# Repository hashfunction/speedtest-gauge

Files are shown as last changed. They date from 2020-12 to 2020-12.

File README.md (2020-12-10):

# Treat Yourself to a Hack Day: Make a Physical Speedtest Gauge

Sure you love taking a Speedtest, but have you ever seen the results manifest in a 3D statue that lives on your desk? Now’s your chance. This repo contains everything you need to construct and program an ethernet-enabled physical Speedtest Gauge. All you’ll need to build it is access to a 3D printer, some affordable and easy-to-find parts, and a basic working knowledge of both electronics and command line interface (CLI) tools. Then you can proudly display your Speedtest gauge on your desk or gift it to a friend who also loves to nerd out over networks. Either way, you’ll have the most fun setup for measuring network throughput in town.

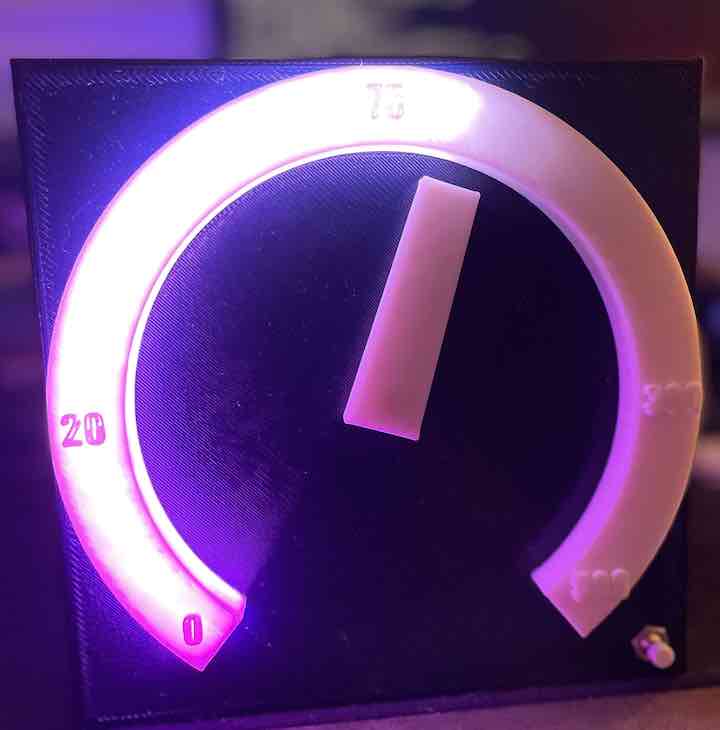
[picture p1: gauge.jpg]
Speedtest Gauge


## Components you’ll need
The total cost of all the components below is around $65, and the project will take about two or three hours to complete, not counting the time to 3D print the enclosure. 

This project requires the following components to work:

* A soldering iron. A basic one should do fine. 
* [Jumper wires](https://smile.amazon.com/REXQualis-120pcs-Breadboard-Arduino-Raspberry/dp/B072L1XMJR) to connect the various components together.
* A stepper motor. This project used [this model](https://smile.amazon.com/ELEGOO-28BYJ-48-ULN2003-Stepper-Arduino/dp/B01CP18J4A/) but feel free to upgrade to a better one. The limitation of this one is that the max speed is slow and so the gauge needle is not very quick.
* Programmable LED lights. This project uses [three neopixel ring lights](https://www.adafruit.com/product/1768). Note that you will need three of these to form the full gauge. You can find cheaper versions of this ring elsewhere.
* Physical buttons. A good candidate for buttons are these [mini push buttons](https://smile.amazon.com/gp/product/B0752RMB7Q/). 
* A [Raspberry Pi](https://www.adafruit.com/category/105). This drives the LED lights as well as the motor and runs the actual test. 
* A good [power source](https://smile.amazon.com/Raspberry-Power-Supply-Off-Switch/dp/B083JCL6H2) for the Raspberry Pi. 
* The 3D-printed housing. The housing and needle are where you finally get to put everything together. The STL printable files can be found on this GitHub project. 
* The free [Speedtest CLI](https://www.speedtest.net/apps/cli). The latest version of the official Speedtest CLI is used to actually run the network performance test. 
* Unbuffer. This is needed to parse the Speedtest CLI output. You can install it by running ```apt-get install expect```

## How to assemble your Speedtest gauge

* Step 1: Print out the housing using a 3D printer. The instructions can be found in this GitHub project. 

* Step 2: Attach the stepper motor to the center of the 3D-printed housing. Then attach the stepper motor driver to the motor, attach the +5V and GND on the controller to the appropriate Raspberry Pi GPIO pin. 

* Step 3: Attach the needle to the tip of the stepper motor. You can snap them together with some glue. 

* Step 4: Connect the controller to the Raspberry Pi with the following GPIO mappings:

    > IN1 to GPIO17
    > IN2 to GPIO22
    > IN3 to GPIO23
    > IN4 to GPIO24

* Step 5: Solder the neopixel rings per [this guide](https://learn.adafruit.com/neopixel-60-ring-clock/circuit-diagram) on Adafruit. Note that we will be using three segments only. After that, connect the +5V and GND on the neopixel lights to the +5V and GND on the Raspberry Pi. Then connect the data line to GPIO18 on the Raspberry Pi. 

* Step 6: Inset the neopixel ring into the gauge indent. You can use sticky tape or soft glue to hold it in place. 

* Step 7: Insert the button in the button hold in the bottom left corner of the front housing. Solder two wires to the connections at the back of the button and attach one lead to GPIO1 (3.3v) on the Raspberry Pi and the other to GPIO10.

* Step 8: Use the extra space in the back where the Raspberry Pi ports are accessible to pass through the power cable and plug it into the Raspberry Pi. 

## Use the software to run Speedtest

The software you’ll need to power your new Speedtest gauge is available on this [GitHub repository](https://github.com/hashfunction/speedtest-gauge) and can be downloaded for non-commercial use. The main sections control the LED lights, the stepper motor and run the CLI test. You can pull this code on the Raspberry Pi and set it to run on startup. Make sure you set the SD Card to read-only mode to prevent data corruption due to reboots.

The following components control the gauge: 

* speedtest.py. This runs the Speedtest CLI app and parses and returns the speed measurements as well as the current stage
* gauge.py. This class takes in the current speed and calculates and moves the needle to the angle represented by the speed. It also lights up the LED based on the position of the needle. 
* button.py. This simple wrapper handles events from the button, which runs the test. 
* run.py. The root file listens to the button events and coordinates between the Speedtest and gauge movement. 

To set up the gauge, load the repo on the device and run the code below. Note that sudo is required to access the GPIO ports on the Raspberry Pi. 

```sudo python3 run.py```

Note that you can use the src/speedtest_bootup.service (change the script location) to always start the software on reboot. 

There you have it! Your very own Speedtest gauge. Share your pictures with us on Twitter or Facebook using the hashtag #SpeedtestGauge.

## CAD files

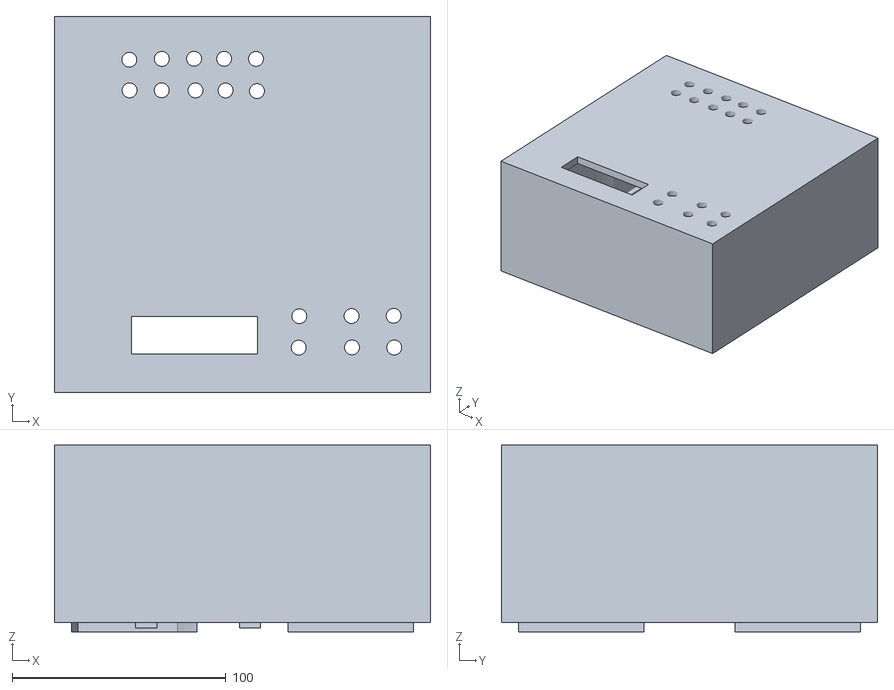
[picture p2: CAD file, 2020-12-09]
3DHousing/back.stl
176.0 x 176.0 x 87.5

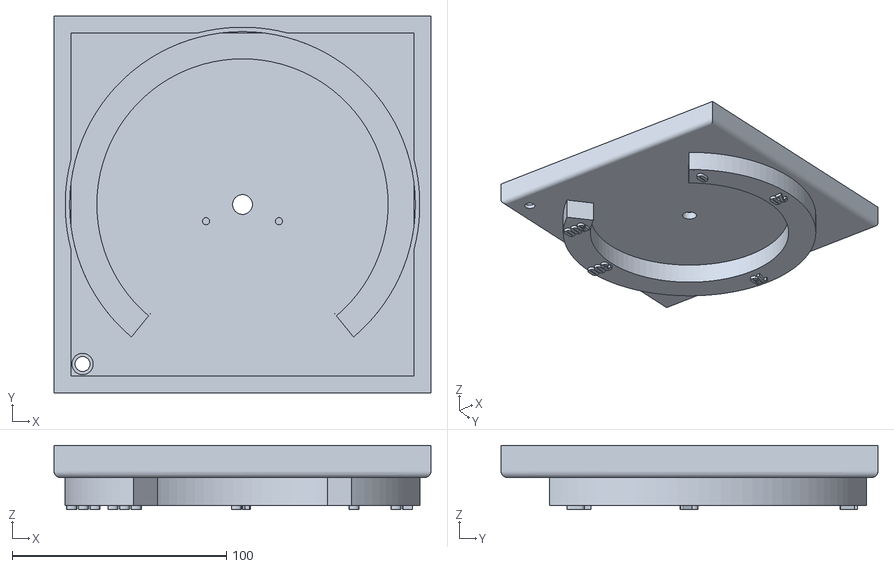
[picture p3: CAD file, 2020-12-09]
3DHousing/front.stl
176.0 x 176.0 x 30.0

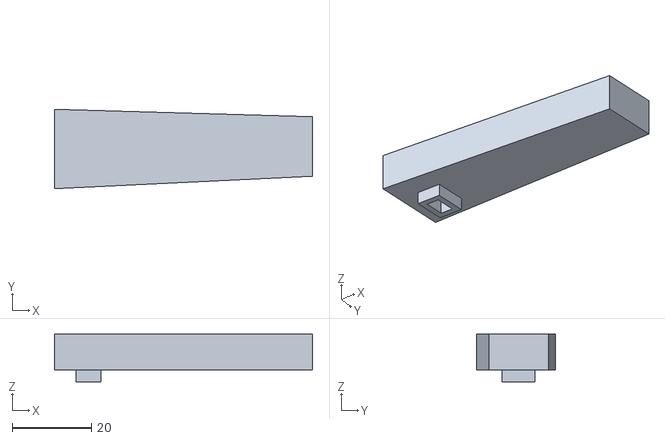
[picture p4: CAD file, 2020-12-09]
3DHousing/needle.stl
65.0 x 20.0 x 12.0

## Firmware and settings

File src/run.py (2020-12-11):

from speedtest import Speedtest
from gauge import Gauge
import os
import sys
from queue import Queue
from threading import Thread
import time
from button import Button
import RPi.GPIO as GPIO
import neopixel
import board

def runTest(neopixels):
    queue = Queue() 
    speedtest = Speedtest(queue)
    speedtest.start()

    gauge = Gauge(neopixels)

    # read speed from test and update gauge
    (stage, speed) = queue.get(True, 10)
    while speed > 0 or not queue.empty():
        try:
            (currentStage, speed) = queue.get(True, 4)

            # move gauge to 0 after the previous stage
            if (currentStage != stage):
                gauge.MoveToMbps(stage, 0)
                gauge.ResetLights()
                time.sleep(1)

            gauge.MoveToMbps(currentStage, speed)
            stage = currentStage
        except Exception:
            break


    speedtest.Complete()
    gauge.Complete()


def main(argv):
    GPIO.cleanup()

    # Single neopixel library instance
    maxPixels = 45
    neopixels = neopixel.NeoPixel(board.D18, maxPixels, brightness=0.5, auto_write=False)

    button = Button()

    while True:
        # check button press blocking with timeout of 3 seconds
        if button.WaitForPress(3000):
            runTest(neopixels)

    button.Complete()

if __name__ == "__main__":
     main(sys.argv[1:])

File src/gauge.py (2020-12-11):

import sys
import time
import RPi.GPIO as GPIO
import array as arr
import time
import board
import neopixel
from stage import Stage

class Gauge:
    pixelPin = board.D18
    numPixels = 45
    # number of degrees each LED light occupies in the ring
    pixelWidthAngle = 6

    gaugeNumbers = arr.array('d',[0, 20, 75,  300, 500])
    gaugeAngles = arr.array('d', [0, 50, 134, 222, 270])

    # Stepper motor settings
    stepPins = [17,22,23,24]

    # motor rated at 4096 steps in 360 degrees
    stepAngle = 360 / float(4096)
    waitTime = 2/float(1000)

    # half step sequence for stepper
    seq = [[1,0,0,1],
       [1,0,0,0],
       [1,1,0,0],
       [0,1,0,0],
       [0,1,1,0],
       [0,0,1,0],
       [0,0,1,1],
       [0,0,0,1]]

    # Color scheme
    downloadGaugeColorA = (1, 163, 229)
    downloadGaugeColorB = (25, 191, 120)

    uploadGaugeColorA = (107, 50, 149)
    uploadGaugeColorB = (233, 123, 206)

    latencyGaugeColorA = (235, 221, 80)
    latencyGaugeColorB = (31, 164, 233)

    def __init__(self, pixels):
        GPIO.setmode(GPIO.BCM)

        self.pixels = pixels

        for pin in self.stepPins:
          GPIO.setup(pin,GPIO.OUT)
          GPIO.output(pin, False)

        self.currentPixelNum = 0
        self.currentPixelAngle = 0
        self.currentAngle = 0
        self.stepCount = len(self.seq)

        self.__ShowColorWheel()

    def __ShowColorWheel(self):
        colorA = self.latencyGaugeColorA
        colorB = self.latencyGaugeColorB
        for i in range (0, self.numPixels):
            self.pixels[i] = (self.__GetColorFromRange(i, 0, self.numPixels, colorA[0], colorB[0]), 
                              self.__GetColorFromRange(i, 0, self.numPixels, colorA[1], colorB[1]), 
                              self.__GetColorFromRange(i, 0, self.numPixels, colorA[2], colorB[2]))
            self.pixels.show()
            time.sleep(0.024)

        for i in range (0, self.numPixels):
            self.pixels[i] = (0,0,0)
            self.pixels.show()
            time.sleep(0.024)

    def __GetColorValue(self, index, currentPixel, stage):
        colorA = self.downloadGaugeColorA if stage is Stage.Download else self.uploadGaugeColorA
        colorB = self.downloadGaugeColorB if stage is Stage.Download else self.uploadGaugeColorB
        return self.__GetColorFromRange(currentPixel, 0, self.numPixels, colorA[index], colorB[index])

    def __GetColorFromRange(self, value, leftMin, leftMax, rightMin, rightMax):
        leftSpan = leftMax - leftMin
        rightSpan = rightMax - rightMin

        valueScaled = float(value - leftMin) / float(leftSpan)
        return int(rightMin + (valueScaled * rightSpan))

    def MoveToMbps(self, stage, speed):
        newAngle = self.__calculateAngleFromMbps(speed)
        # bail if the difference is small to prevent needle from jittering
        if (abs(self.currentAngle - newAngle) < 6):
            return

        stepCounter = 0
        stepAngleCurrent = 0

        dir = -1 if self.currentAngle > newAngle else 1
        shouldBreak = False

        # move the needle and colors to the right place
        while True:
          for pin in range(0, 4):
            xpin = self.stepPins[pin]
            if self.seq[stepCounter][pin]!=0:
              GPIO.output(xpin, True)
            else:
              GPIO.output(xpin, False)

          #increment angle for 1 step
          self.currentAngle += self.stepAngle * dir
          #set to next step
          stepCounter += dir

          self.__updateLights(dir, stage)

          if (dir < 0 and self.currentAngle <= newAngle):
              shouldBreak = True
          elif (dir > 0 and self.currentAngle > newAngle):
              shouldBreak = True

          if (stepCounter>=self.stepCount):
            stepCounter = 0
            if shouldBreak:
                break
          if (stepCounter<0):
            stepCounter = self.stepCount+dir
            if shouldBreak:
                break

          # Wait before moving on
          time.sleep(self.waitTime)

    def __updateLights(self, dir, stage):
        if (abs(self.currentAngle - self.currentPixelAngle) >= self.pixelWidthAngle):
            self.pixels[self.currentPixelNum] = (self.__GetColorValue(0, self.currentPixelNum, stage), self.__GetColorValue(1, self.currentPixelNum, stage), self.__GetColorValue(2, self.currentPixelNum, stage)) if dir == 1 else (0,0,0)

            self.pixels.show()
            self.currentPixelNum += dir
            self.currentPixelNum = min(self.numPixels-1, self.currentPixelNum)
            self.currentPixelAngle = self.currentAngle

    def __calculateAngleFromMbps(self, mbps): 
      if (mbps <= 0):
        return self.gaugeAngles[0]

      indexLow = 0
      for i in range(len(self.gaugeNumbers)):
        if (self.gaugeNumbers[i] > mbps):
          indexLow = max(0, i-1)
          break

      indexHigh = min(len(self.gaugeAngles), indexLow+1)
      A = self.gaugeNumbers[indexLow]
      B = self.gaugeNumbers[indexHigh]
      C = self.gaugeAngles[indexLow]
      D = self.gaugeAngles[indexHigh]

      angle = C + (mbps - A) * (D - C) / (B - A)
      angle = min(angle, self.gaugeAngles[len(self.gaugeAngles)-1])
      
      return angle

    def Complete(self):
        self.MoveToMbps(Stage.Upload, 0)
        self.ResetLights()

    def ResetLights(self):
        for i in range(0, self.numPixels):
            self.pixels[i] = (0,0,0)

        self.pixels.show()

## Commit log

2020-12-07 Adding STL files for 3d printed housing
    [back.stl, front.stl, needle.stl]
2020-12-09 Updated 3D housing with minor alignment fixes
    [back.stl, front.stl, needle.stl]
2020-12-09 Add a color wheel during latency selection
2020-12-09 Added script to start after reboot
    [gauge.py, run.py, speedtest.py]
2020-12-10 fixed issue with upload speed not showing all the way
    [run.py]
2020-12-11 fix issue with color range
    [gauge.py]
